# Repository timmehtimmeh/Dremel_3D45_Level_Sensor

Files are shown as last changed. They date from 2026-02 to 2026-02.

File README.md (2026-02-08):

# Dremel_3D45_Level_Sensor
KiCAD project, schematic, and gerbers of a Printed Circuit Board (PCB) replacement for The Auto_LevelBoard PCB for the Dremel 3D45 (and possibly the Dremel 3D40)
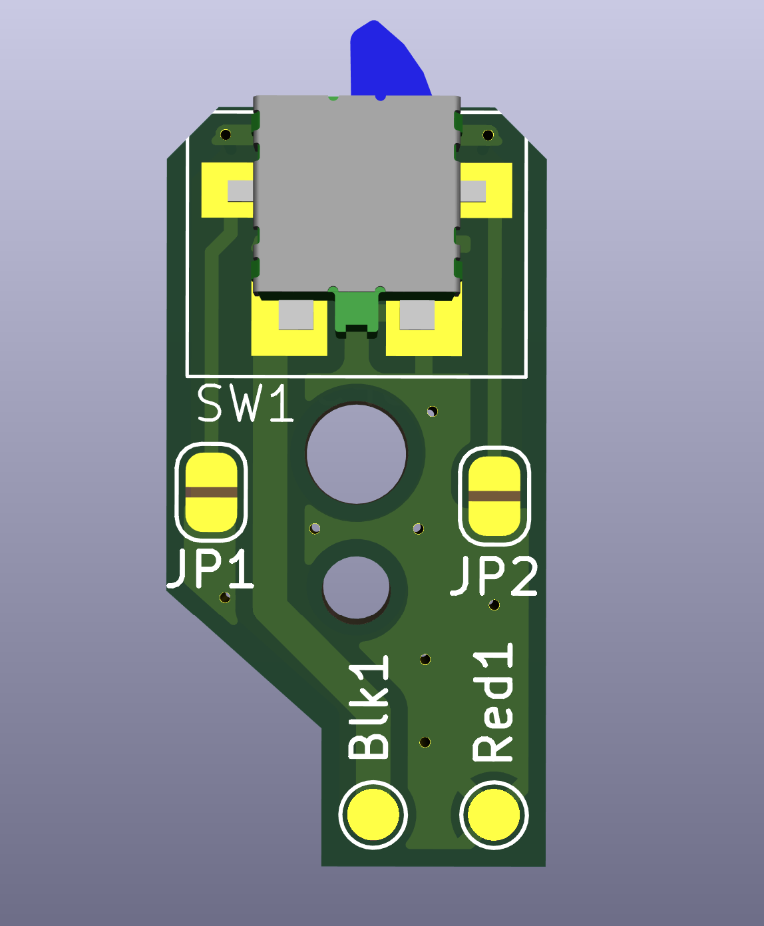
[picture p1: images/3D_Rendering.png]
PCB Rendering Rendering of the PCB
  **NOTE** Using this PCB will likely void any warranty provided with the printer.  An entire replacement leveling arm assembly can be [purchased directly from 3PITech](https://3pitech.com/products/3d45-leveling-sensor)

# Getting the Gerbers
If you only want to have the PCBs manufactured, navigate to the [releases page](https://github.com/timmehtimmeh/Dremel_3D45_Level_Sensor/releases/) and download the zip file of the gerbers

# Cloning the repo
This repository references the KiCAD symbol and footprint libraries stored in [Tims-KiCad-Library](https://github.com/timmehtimmeh/Tims-KiCad-Library) to properly clone this repo please type the following into a git command window:

```git clone --recurse-submodules https://github.com/timmehtimmeh/Dremel_3D45_Level_Sensor.git```

# Parts required

The following parts are required to replace the PCB

| Part | Qty | Link | Notes|
|------|-----|------|------|
| PCB | 1 | I had the gerbers successfully manufactured at [JLCPCB](https://jlcpcb.com/) as well as [OSHPark*](https://oshpark.com/shared_projects/k3kUrSLB) | * **NOTE:** The original Dremel PCB is 1mm thick.  OshPark only makes standard thickness 1.6 mm boards, but the thicker 1.6mm board worked fine in the printer. JLCPCB has options for 1mm thick boards |
| Switch | 1 | The OEM seems to be a [Panasonic ESE-31R15T](https://www.digikey.com/en/products/detail/panasonic-electronic-components/ESE-31R15T/3163183) | An alternate can be the [TE Connectivity JJJHRGG200NOPMRTR](https://www.digikey.com/en/products/detail/te-connectivity-alcoswitch-switches/JJJHRGG200NOPMRTR/9452492), but in testing the Panasonic part was less prone to getting stuck in the housing |
| Jumper Wire | 2  | [Wire](https://www.amazon.com/dp/B089CWGQKW) |  The OEM is 26 AWG stranded wire, 90 mm, 1 red, one black Outer Diameter (O.D) 1mm. I used the 1.2 mm O.D. 28 AWG silicone coated wire linked, and it still fits inside the cable routing cutouts on the level arm. |
| 2 Position JST-PH 2mm Connector | 1 | [JST Kit](https://www.amazon.com/dp/B0F485CN38) | I used the kit linked, however you can also buy pre-assembled wires  |

Additionally Soldering equipment (iron, solder), and either Silicone glue, or Hot Glue are needed to complete the job.

# Assembly Instructions

Tools Needed
1.  2mm Hex bit or Hex wrench (Allen key)
2.  T10 Torx (star) screwdriver
3.  T7 Torx (star) screwdriver
4.  Replacement PCB

Once you have gathered the necessary components, assembly is relatively straightforward.
1. Place the switch onto the PCB such that the alignment holes in the bottom of the switch mate with the holes in the PCB
2. Ensure that the switch is centered and square to the board
3. Solder on one of the four pads of the switch.
4. Check Alignment of the switch.  If it's moved heat up the one pad and move the switch until it's square with the board and then let the solder cool
5. Solder the remaining three pads of the switch
6. (Optional) Solder the two jumper pads such that the jumpers make contact. This connects the switch housing to one leg of the switch.  If using the TE Connectivity switch there is no metal housing and this step can be skipped.  If using the Panasonic switch then the circuit will work with or without the jumpers connected together.
7. Strip approximately 2mm of insulation off of one end of each of a black and red wire.
8. Crimp JST-PH connectors onto each of the wires
9. Push the crimped end into a two position JST-PH connector (the red/black orientation doesn't matter, but I kept mine the same as the original board)
10. Cut the wires such that they're both equal in length, and the same length as the OEM wire (approximately 90mm)
11. Strip 2-3mm of insulation off the cut end of the wire
12. Solder the red wire onto the PCB where the silkscreen indicates the red wire should go
13. Solder the black wire onto the PCB where the silkscreen indicates the black wire should go
14. Place the board on something that will allow you to put some silicone or hot glue onto the wires & board
15. Put a blob of glue such that it covers the two soldered ends of the wire and travels a bit up the wire to provide some strain relief.  Be sure to not allow too much glue to blob on the back side of the PCB
16. Once the glue is set, follow Steps 1, 2, and 5 from [these instructions](https://cdn.shopify.com/s/files/1/0552/1797/9558/files/3d45-3d40-leveling-arm-replacement.pdf)
17. Unscrew the PCB from the leveling arm assembly on your printer, taking care to not lose the screw or washer that holds the PCB in place
18. Carefully pull the wires out of the plastic wire guide on the leveling arm assembly, and remove the old PCB from the assembly
19. Thread the JST-PH connector from the new PCB through the appropriate area in the 3D printer head assembly and attach it to the printer, re-attach the servo motor wire if it was disconnected
20. Place the PCB into the sensor arm such that the plastic locating pin holds the PCB in place.
21. Using the T7 torx screwdriver, attach PCB using the screw & washer that was taken out in Step 17.
22. Reassemble the Extruder by following Step 6 in [these instructions](https://cdn.shopify.com/s/files/1/0552/1797/9558/files/3d45-3d40-leveling-arm-replacement.pdf)
23. If necessary, calibrate the level arm up/down position by navigating to TOOLS>SETTINGS>SERVICE TOOLS>LEVELING SWITCH and set the level (Step 7 in the linked instructions)
24. Calibrate the nozzle gap by following [these instructions](https://www.dremel.com/binaries/content/assets/dremel/uk/digilab/how-to-self-repair/3d45/3d45-nozzle-gap-calibration.pdf)

**Notes** - After a few uses I found that the replacment switch was not rebounding as quickly as it should.  To fix this i used a little bit of nonconductive spray lubricant on the tip of the switch and moved the switch in and out a few times after which the switch rebounded much more quickly.

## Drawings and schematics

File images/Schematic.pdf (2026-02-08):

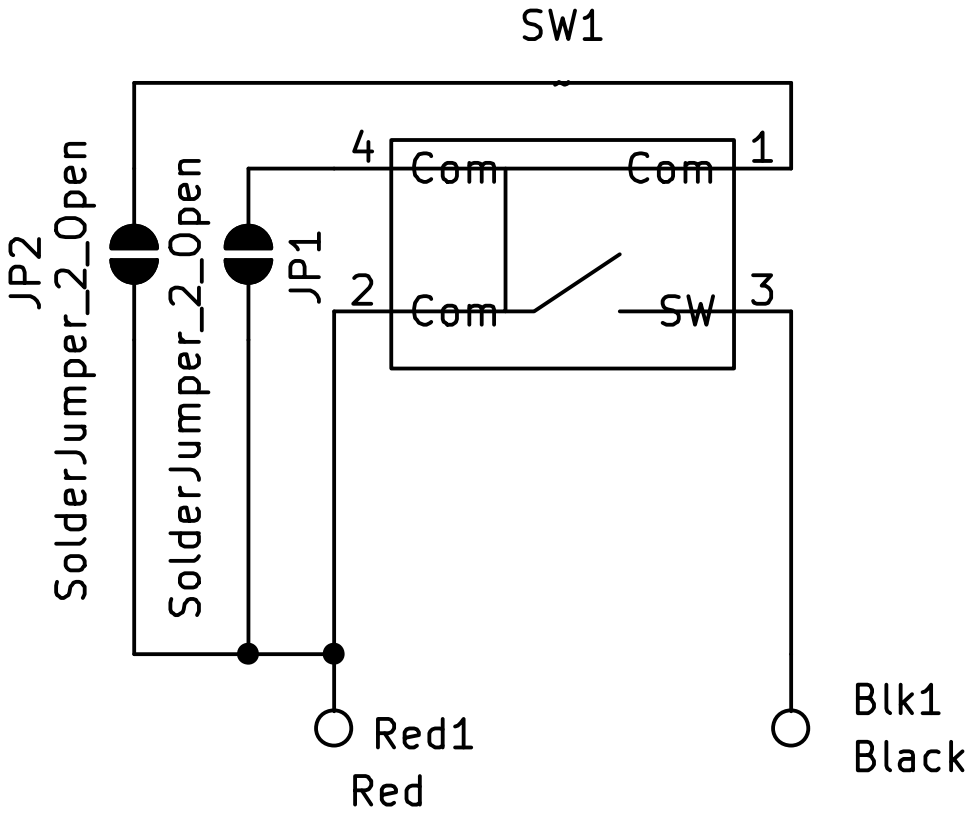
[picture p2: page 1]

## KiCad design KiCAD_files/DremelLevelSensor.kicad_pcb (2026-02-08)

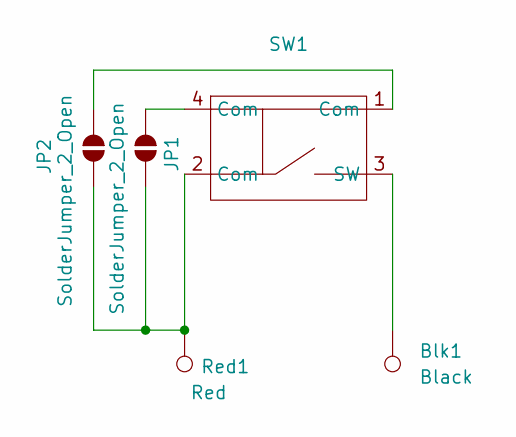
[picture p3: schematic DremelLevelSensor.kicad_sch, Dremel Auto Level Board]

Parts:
Blk1: Black; TestPoint_Pad_D1.5mm
JP1, JP2: SolderJumper_2_Open; SolderJumper-2_P1.3mm_Open_RoundedPad1.0x1.5mm
Red1: Red; TestPoint_Pad_D1.5mm
SW1: ESE31R11T

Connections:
GND: JP1.1 (A), JP2.1 (A), Red1.1, SW1.2 (Com)
unnamed: JP1.2 (B), SW1.4 (Com)
unnamed: JP2.2 (B), SW1.1 (Com)
unnamed: Blk1.1, SW1.3 (SW)

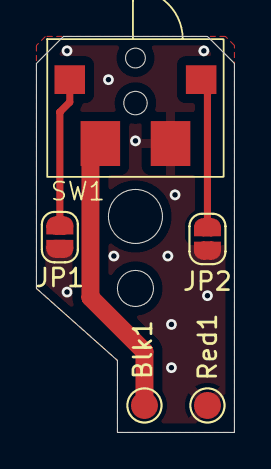
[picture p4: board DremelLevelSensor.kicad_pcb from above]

Board: 2 copper layers, 11.0 x 22.0 mm, 5 parts (0 on the bottom side), 4 nets.

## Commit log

2026-02-08 Update README to include KiCAD project details
2026-02-08 Add KiCad files
    [DremelLevelSensor.kicad_pcb, DremelLevelSensor.kicad_sch]
2026-02-08 Add kicad gitignore file
2026-02-08 fix text in wire section
2026-02-08 Update PCB and Schematic to remove unnecessary jumper that was added to try to get DKRed to work
    [DremelLevelSensor.kicad_pcb, DremelLevelSensor.kicad_sch]
2026-02-08 Move KiCAD Files folder, add pdf of schematic
    [DremelLevelSensor.kicad_pcb, DremelLevelSensor.kicad_sch]
2026-02-08 Add Footprint & Symbol library as git submodule. Reference the footprint & symbols as project specific libraries
